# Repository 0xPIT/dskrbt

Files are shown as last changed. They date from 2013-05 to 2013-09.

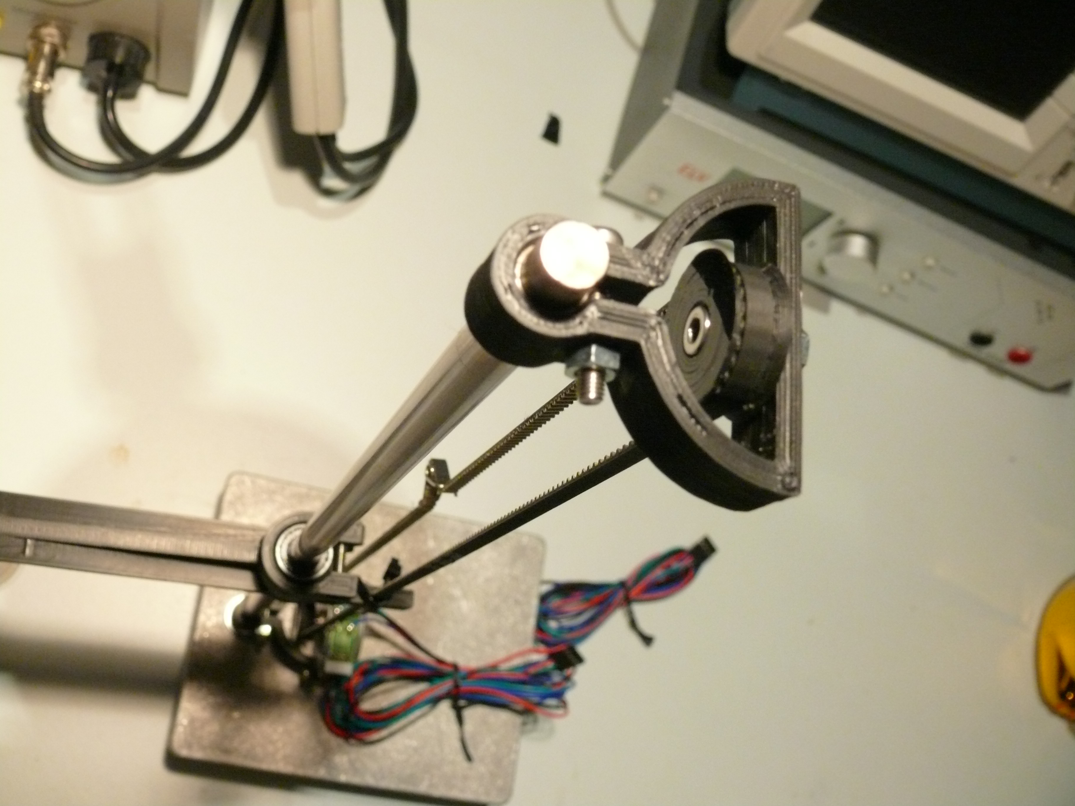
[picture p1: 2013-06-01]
photos/P1020513.JPG

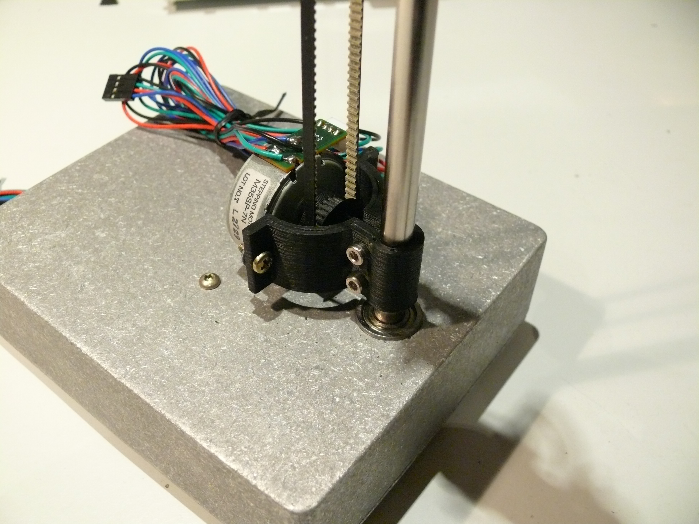
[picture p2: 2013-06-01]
photos/P1020511.JPG

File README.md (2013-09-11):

# dskrbt

As Simple as Possible CD/ DVD Disk Changer Robot

`This is a work in progress`

#### License

<br />This work is licensed under a <a rel="license" href="http://creativecommons.org/licenses/by-nc-sa/3.0/deed.en_US">Creative Commons Attribution-NonCommercial-ShareAlike 3.0 Unported License</a>.

#### Project sources

- https://github.com/0xPIT/dskrbt
- http://www.thingiverse.com/thing:97291

### What?

I intend to archive all of my several hundred audio CDs to gain shelf space. So I try to build a small robot capable of changing the disks that

- uses as few parts as possible
- can be built from cheap, standard or scrap-, plus some 3D printed parts
- is of small size so that it can be stowed away easily

Status
Status

### Design

Like most commercial units, I believe that a beam with a grabber mechanism should work best and helps to get a rather small unit. I was thinking about a suitable mechanism for grabing, that is easy to build but found no satisfactory solution. There's a project available using a carved wooden grabber with a solenoid, but thats too fragile in my opinion, also probably heavy. After finding cheap industrial vacuum cups on ebay (10€), I decided to go with that.

#### Parts used (so far)

- 8mm rod from old printer
- GT2 timing belt from old scanner for Z axis
- smaller GT2 timing belt for X (rotational) axis
- 3D-printed belt pulleys
  - find several openscad pulleys on thingiverse
- ball bearings, one flanged (F688ZZ), one normal (608)
- tiny ball bearing pressed into the idler pulley
- 3D-printed bearing holder (inside enclosure)
- cheapo aluminum enclosure
- industrial vacuum cup with spring [ebay](http://www.ebay.de/itm/160774763977) + [ebay](http://www.ebay.de/itm/160776083251)
- two stepper motors from old scanners
  - Mitsumi M35SP-7N, 4 Ohms, set to ~500mA
  - Motor pinions fit GT2 belt
- [Crumbuino](http://chip45.de/products/crumbuino-nano_arduino_compatible_atmega328_module_board_usb.php), similar to an Arduino Nano
- 2 pololu / StepStick stepper controller [ebay](http://www.ebay.de/itm/280877891763)
- [grbl](https://github.com/grbl/grbl) 0.9x to control the beast

### Issues & Todo

- Find a nice, simple way to sense that the arm has arrived at the stack of CDs while moving down the z-axis. 
  - The vacuum cup has a spring, probably add some optical or hall sensor to detect when the spirng engages? (could be too much force, though)

- Homing
  - X-Axis: Add a magnet on the motor and a Hall Sensor
  - Z-Axis: Hall or optical?

- Modify grbl and add a G-Code (M66?) so that, while picking up or dropping of a disc the arm's z-axis can move an arbitrary distance, depending on the size of stack of discs left to pick up or already dropped off.
 
- Need a method on how to detect the presence of a disk. Current draft idea is to use CNY70 refelctive optical sensor. Should simply trigger an interrrupt and send some short ascii token via the serial connection.

- The linear bearing (LM8UU) does not like the forces indiced by the changer arm and sometimes gets stuck. This is probably due to my bearing being a cheap chinese type. Use a brass or sintered bronce bearing?

- In order to save parts and a second rod, I intended the arm to be stabilized rotationally only by the belt. this is very inaccurate, the arm wiggles. could work, though.

- The vacuum cup just needs a pneumatic solenoid valve to hold a CD, i.e. no vacuum is necessary, but it wont hold for long. Therefore, I plan to use a tiny vacuum pump nevertheless.

### Status
- 2013-08-27
  - avr & pololus replaced, devised simple robot arm calibration strategy
- 2013-05-31
  - tested mechanics with grbl. works nicely. Set motors to ~500mA each.
  - messed with the cables: fried avr and pololus (got 12V on VDD)
  - Ordered replacements
- 2013-05-30
    - completed mechanical prototype

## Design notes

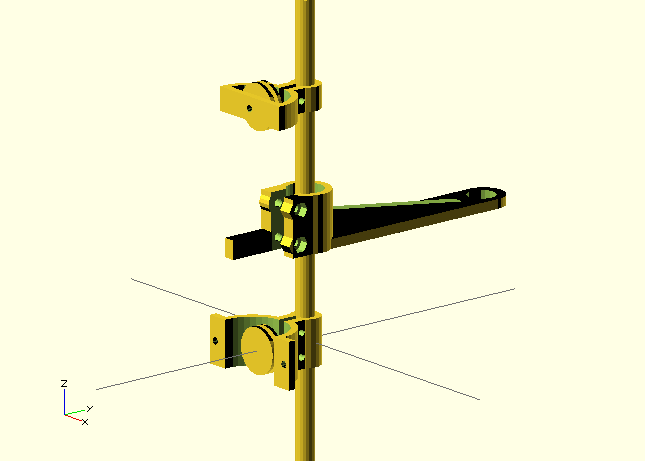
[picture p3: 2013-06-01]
mechanical/dskrbt.rendering.png

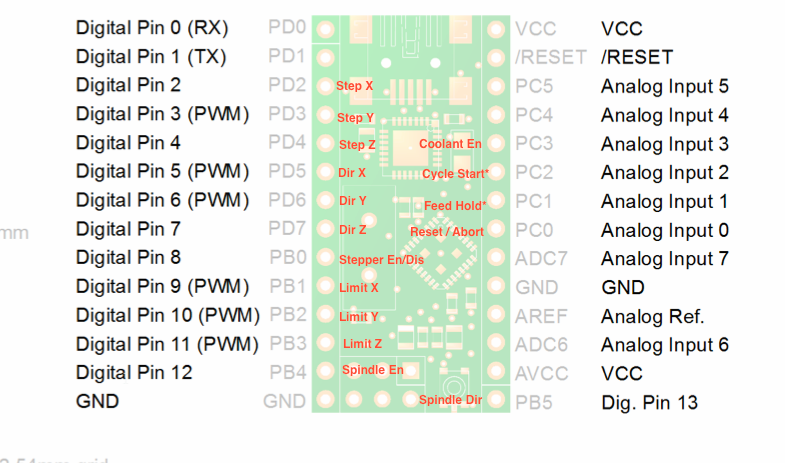
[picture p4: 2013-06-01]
misc/Crumb grmbl Pins.png

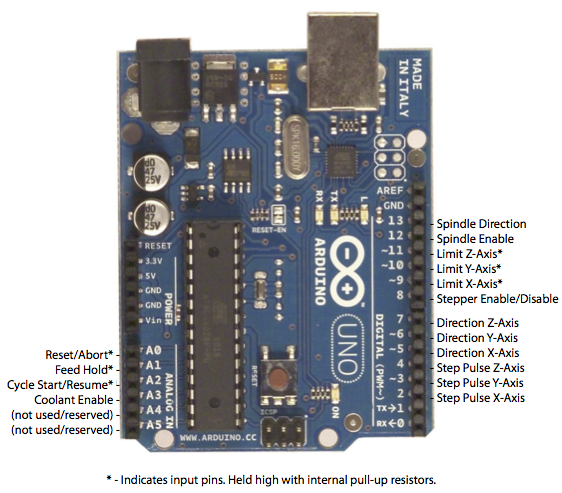
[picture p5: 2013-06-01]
misc/Grbl_Pin_Diagram.png

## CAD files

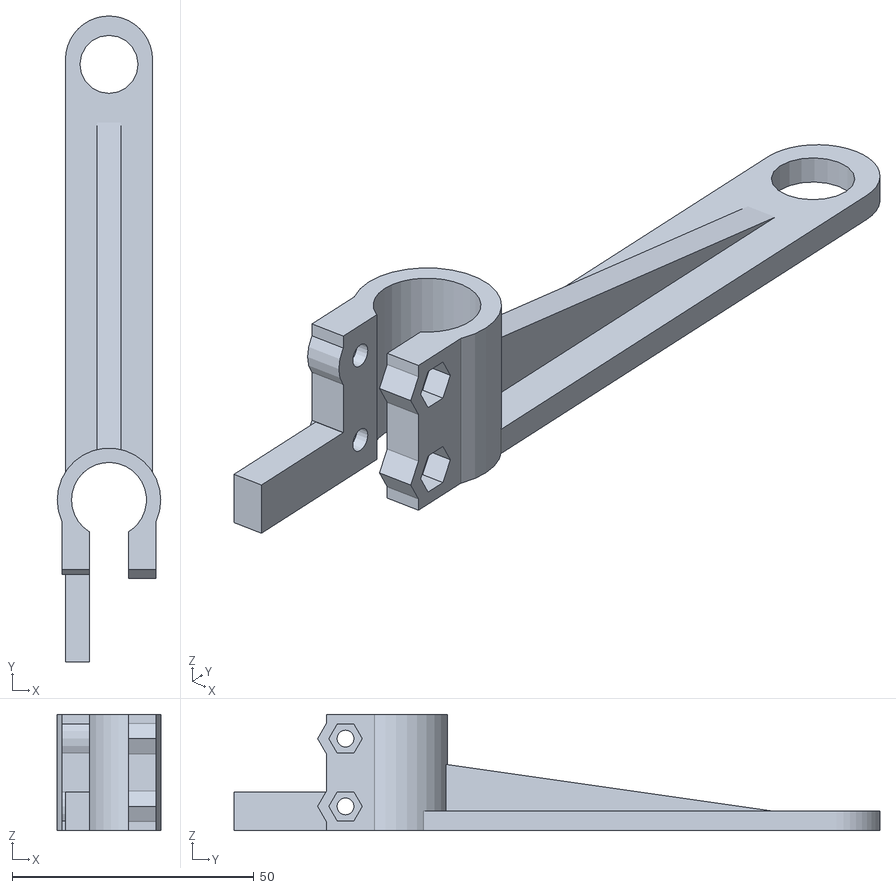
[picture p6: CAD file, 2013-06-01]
misc/carriage.stl
21.4 x 133.5 x 24.0

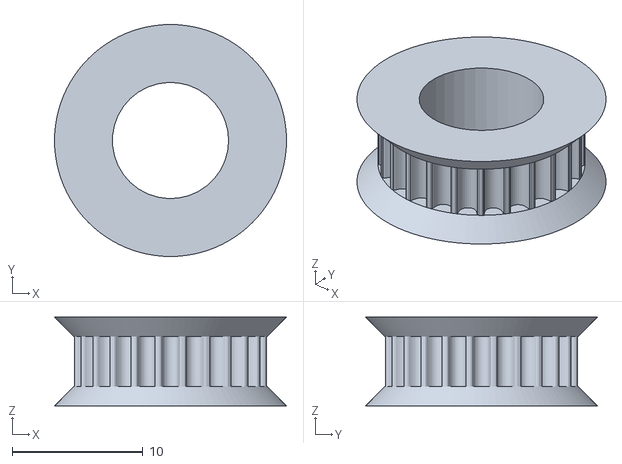
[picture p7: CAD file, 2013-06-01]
misc/PulleyMotor.stl
17.8 x 17.8 x 6.80

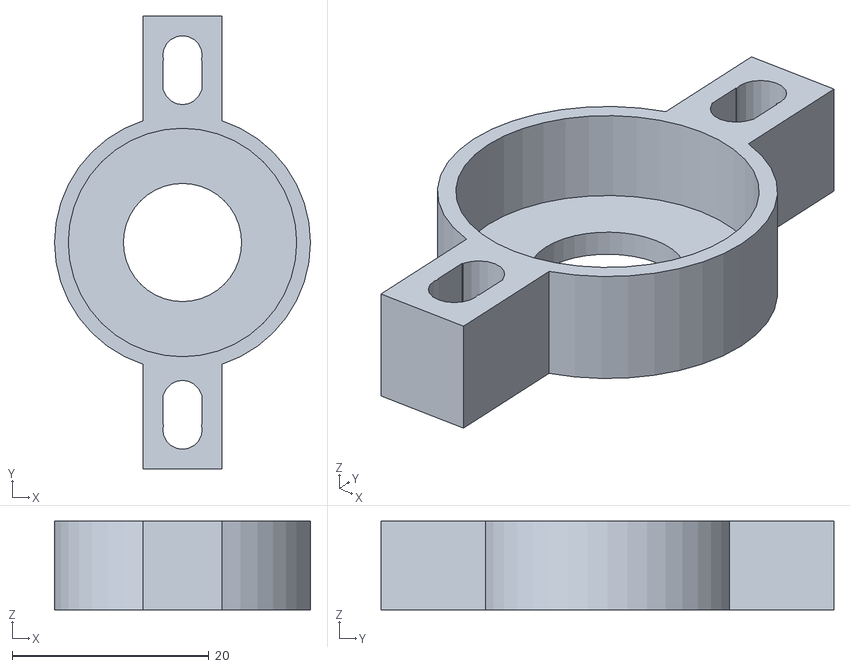
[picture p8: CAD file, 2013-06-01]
misc/608mount.stl
26.0 x 46.0 x 9.00

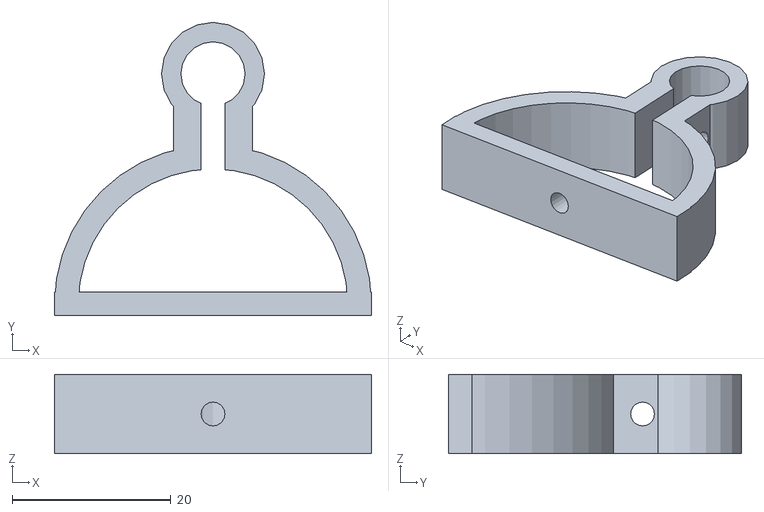
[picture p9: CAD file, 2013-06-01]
misc/mount_top.stl
40.0 x 37.0 x 10.0

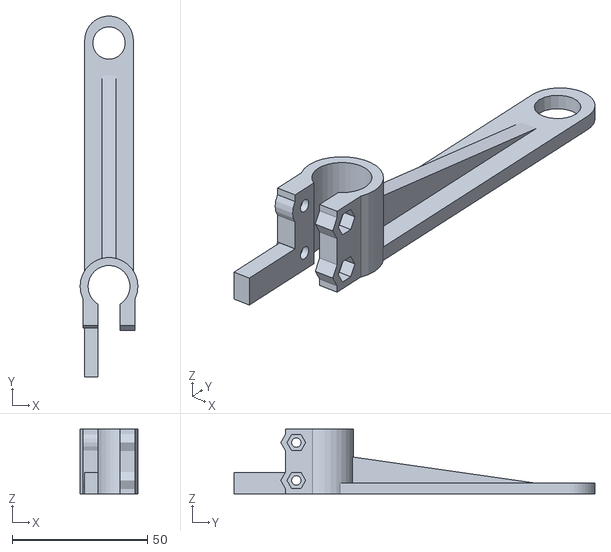
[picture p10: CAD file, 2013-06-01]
misc/carriage_fixed.stl
21.4 x 133.5 x 24.0

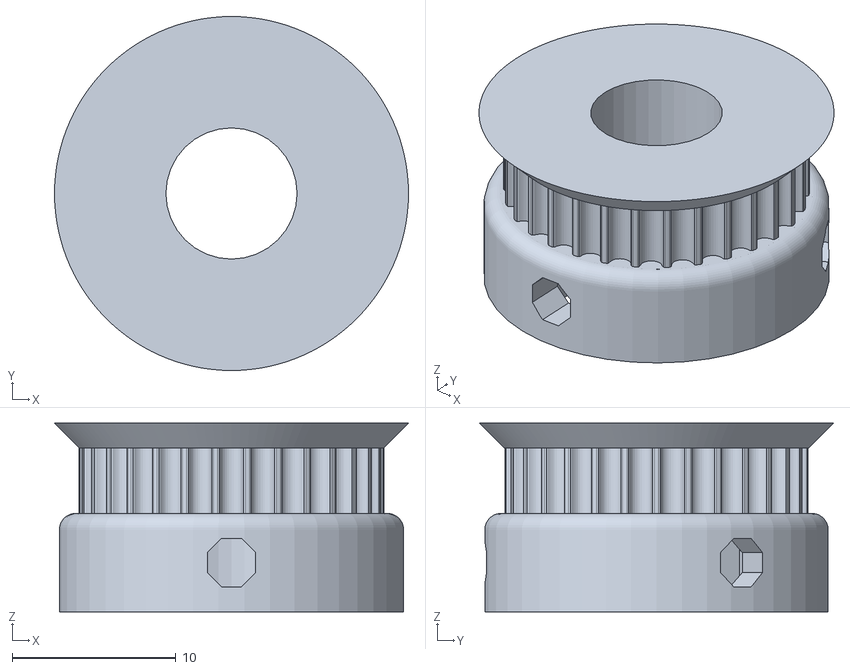
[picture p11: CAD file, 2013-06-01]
misc/Pulley_GT2_30T_8mm.stl
21.6 x 21.6 x 11.5

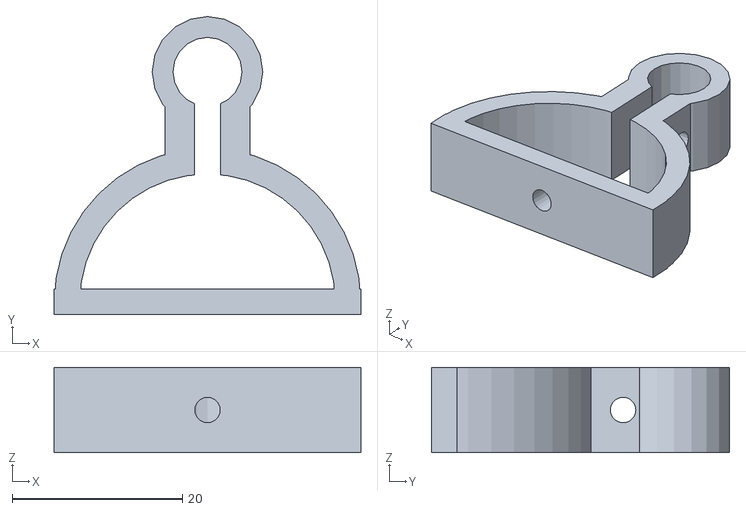
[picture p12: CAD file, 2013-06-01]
misc/mountIdler.stl
36.0 x 35.0 x 10.0

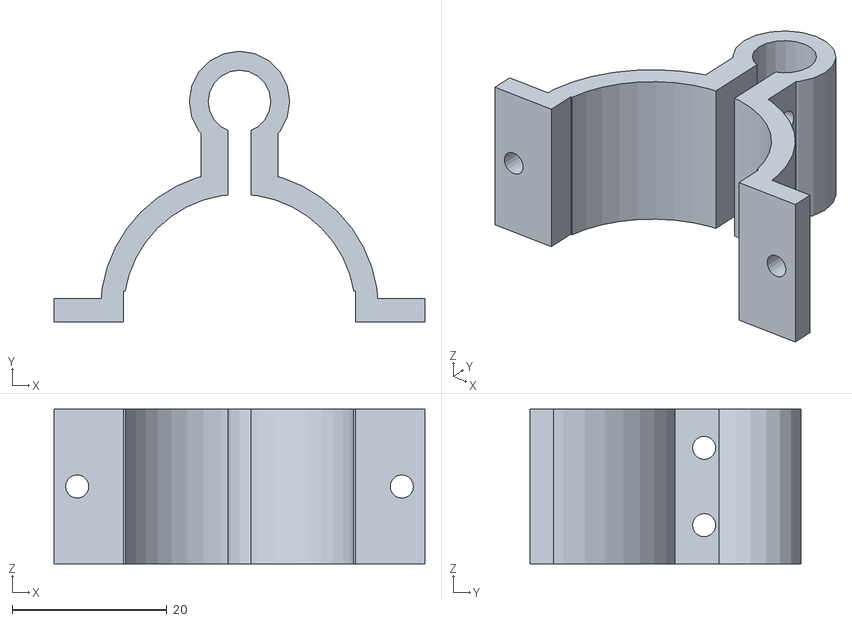
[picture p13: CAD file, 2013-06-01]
misc/mountMotor.stl
48.0 x 35.0 x 20.0

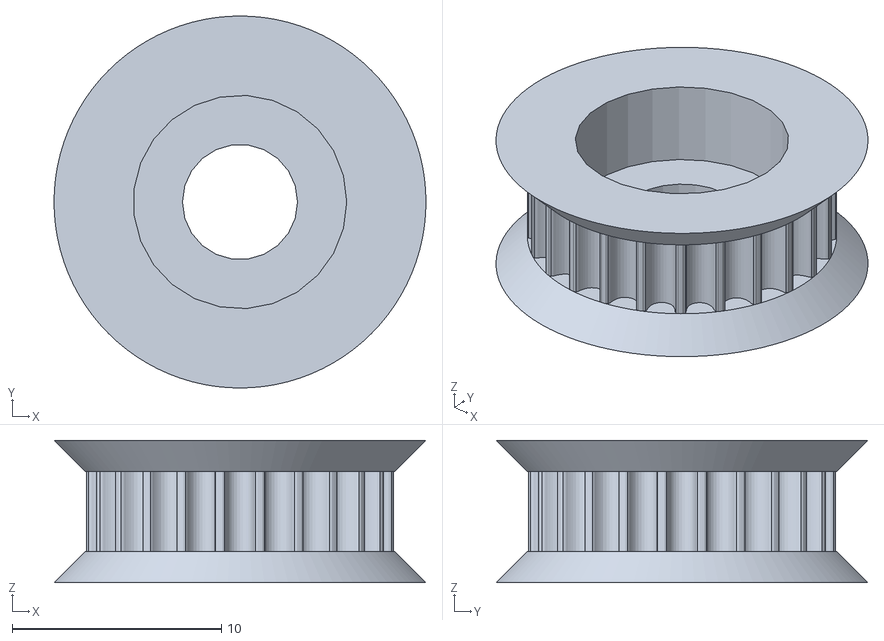
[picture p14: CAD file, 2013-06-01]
misc/PulleyIdler.stl
17.8 x 17.8 x 6.80

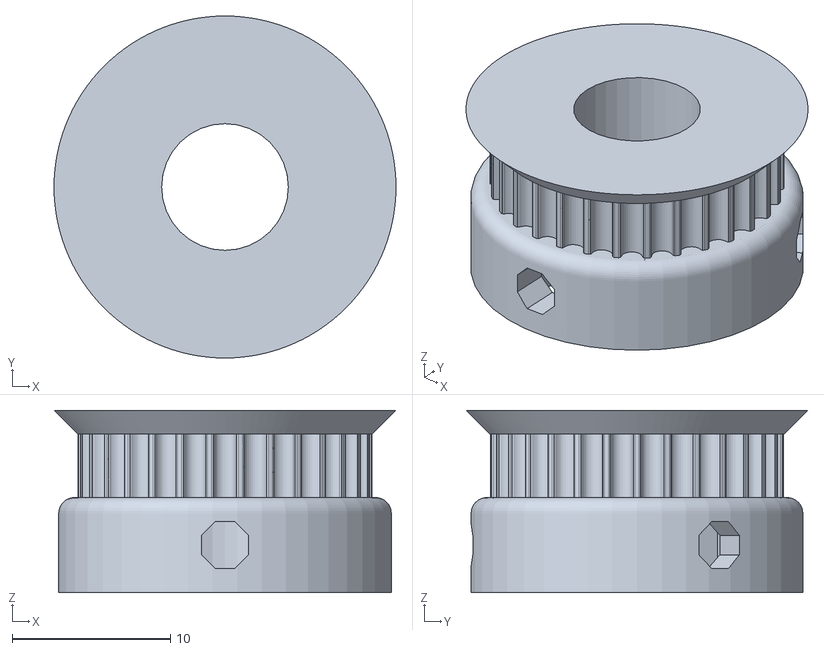
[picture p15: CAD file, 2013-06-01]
misc/PulleyGT230T8mm_fixed.stl
21.6 x 21.6 x 11.5

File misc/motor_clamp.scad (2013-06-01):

$fa = 12;
$fs = 0.5;

w = 60; // Smooth rod distance (center to center)

module screws() {
  for (x = [-w/2, w/2]) {
    translate([x, 0, 0]) {
      // Push-through M3 screw hole.
      translate([0, -6, 0]) rotate([0, 90, 0])
	cylinder(r=1.65, h=20, center=true);
      // M3 nut holder.
      translate([-x/5, -6, 0])
	rotate([30, 0, 0]) rotate([0, 90, 0])
	cylinder(r=3.3, h=2.3, center=true, $fn=6);
    }
  }
}

module bracket(h) {
  difference() {

    union() {
      translate([0, -1, 0]) cube([w+12, 22, h], center=true);
      // Sandwich mount.
      translate([-w/2, 10, 0]) cylinder(r=6, h=h, center=true);
      translate([w/2, 10, 0]) cylinder(r=6, h=h, center=true);
    }

    // Sandwich mount.
    translate([-w/2, 12, 0]) cylinder(r=1.9, h=h+1, center=true);
    translate([w/2, 12, 0]) cylinder(r=1.9, h=h+1, center=true);

    // Smooth rod mounting slots.
    for (x = [-w/2, w/2]) {
      translate([x, 0, 0]) {
      	cylinder(r=3.1, h=h+1, center=true);
	    translate([0, -10, 0]) cube([2, 20, h+1], center=true);
      }
    }

    // Belt path.
    translate([0, -5, 0]) cube([w-20, 20, h+1], center=true);
    translate([0, -9, 0]) cube([w-12, 20, h+1], center=true);
    translate([-w/2+10, 1, 0]) cylinder(r=4, h=h+1, center=true);
    translate([w/2-10, 1, 0]) cylinder(r=4, h=h+1, center=true);
  }
}

translate([0, 0, 10]) 
difference() {
bracket(20);
screws();
}

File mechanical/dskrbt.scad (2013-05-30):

// ----------------------------------------------------------------------
// Disk Changer Robot
// github.com/0xPIT/dskrbt
// (c) 2013 karl@pitrich.com
// Insert Creative Commons License Terms Here
// 
// Credits:
//   * modified LM8UU holder by Jonas Kühling
// ----------------------------------------------------------------------

include <./MCAD/shapes.scad>
include <./MCAD/regular_shapes.scad>
include <./MCAD/boxes.scad>

aluminum = [0.9, 0.9, 0.9];
steel = [0.8, 0.8, 0.9];


LM8UU_dia = 15.4; // must be wider than bearing and adjust for printer
LM8UU_length = 24;
rod_dia = 6;

//screw/nut dimensions (M3) - hexagon socket head cap screw ISO 4762, hexagon nut ISO 4032
screw_thread_dia_iso = 3;
screw_head_dia_iso = 5.5;
nut_wrench_size_iso = 5.5;

// screw/nut dimensions for use (plus clearance for fitting purpose)
clearance_dia = 0.5;
screw_thread_dia = screw_thread_dia_iso + clearance_dia;
screw_head_dia = screw_head_dia_iso + clearance_dia;
nut_wrench_size = nut_wrench_size_iso + clearance_dia;
nut_dia_perimeter = (nut_wrench_size/cos(30));
nut_dia = nut_dia_perimeter;
nut_surround_thickness = 2;

// main body dimensions
body_wall_thickness = 2;
body_width = LM8UU_dia + (2*body_wall_thickness);
body_height = body_width;
body_length = LM8UU_length;
gap_width = rod_dia + 2;
screw_bushing_space = 1;

screw_elevation = LM8UU_dia + body_wall_thickness + screw_thread_dia / 2 + screw_bushing_space;

motor_holes    =  42;
arm_length     =  100;
stabilizer_pos = -60;
mount_length   =  60;

module carriage() {
  union() 
  {
    translate([0, LM8UU_dia/2 + body_wall_thickness, 0])
      rotate([90, 0, 0]) 
        lm8uu_holder();

    difference() {
      union() {
        translate([0, (arm_length / 2) - 4.5, -LM8UU_length/2 + 2])
          cube([18, arm_length - 9, 4], center=true);
        
        translate([0, arm_length - 9, -LM8UU_length/2 + 2]) 
          cylinder(r=9, h=4, center=true, $fn=40);
        
        // arm stabilizer
        translate([0, 8, -8])
          rotate([90, 0, -90])
            rightTriangle(arm_length/100*70, 10, 5);
      }

      // cut out inner cylinder
	  translate([0, 0, -(LM8UU_length + 1) / 2]) 
        polyhole(LM8UU_dia, LM8UU_length + 1);

      // payload bore
      translate([0, arm_length - 10, -10])
        cylinder(r=6, h=10, center=true, $fn=20);
    }

    difference() {
      union() {
        translate([-6.5, -23.5, -LM8UU_length/2 + 4])
          cube([5, 20, 8], center=true);
        //translate([-4, stabilizer_pos, -LM8UU_length/2 + 4])
        //  cube([8, 8, 8], center=true);
      }
      //translate([-4, stabilizer_pos, -8])
      //  cylinder(r=1.5, h=10, center=true, $fn=20);
    }
  }
}


module edgeMount(height, upper=false) 
{
  difference() {
    union() {
      cylinder(r=6.5, h=height, center=true, $fn=20);

      for(i = [3, -3])
        translate([i, -5, 0])
          cube([4, 10, height], center=true);

      translate([0, -27, 0]) 
        union() {
          intersection() {
            cylinder_tube(20, 18, 3, center=true, $fn=40);
            translate([0, 10, 0])
              cube([50, 20, height], center=true);
          }

		  if (upper)
            cube([18 * 2, 3, height], center=true);
          if (!upper)
            cube([motor_holes+6, 3, height], center=true);          
        }
    }

    // clamp screw mount holes
    for(i=[height / 2 - 5, -height / 2 + 5])
      translate([0, -6, i])
        rotate([0, 90, 0])
          cylinder(r=1.5, h=15, center=true, $fn=20);

    // rod bore
    cylinder(r=4.05, h=height, center=true, $fn=20);

    // split
    translate([0, -10, 0]) cube([3, 20, height], center=true); 
    if (!upper) {
      translate([0, -27, 0]) cube([18 * 2 - 6, 5, height], center=true);
      translate([0, -40, 0]) rotate([90, 90, 180]) motor42(false);
    }
    else { // upper: bore for pulley
      translate([0, -30, 0]) rotate([90, 0, 0]) cylinder(r=1.5, h=10, center=true, $fn=20);
    }
  }  
}


module motor42(with_body = true) {
    if (with_body)
      cylinder(r=21, h=16, center=true, $fn=20);

    // motor mount holes
    for(i=[motor_holes/2, -motor_holes/2])
      translate([0, i, 10])
          cylinder(r=1.5, h=10+2, center=true, $fn=20);

    // motor shaft hole
    translate([0, 0, 10])
        cylinder(r=5, h=10+2, center=true, $fn=20);
}


module motorCutOut() {  
  difference() {
    cylinder(r=17, h=6, center=true, $fn=20);
    cylinder(r=10, h=6, center=true, $fn=20);
    cube([40, 6, 4] ,center=true);
    cube([6, 40, 4] ,center=true);
  }
}


module rods() {
  // main rod
  translate([0, 0, -60])  color(steel) cylinder(r=4, h=200, center=false, $fn=20);

  // stabilizer rod
  //translate([-4, stabilizer_pos, -60])  color(steel) cylinder(r=1.5, h=400, center=false, $fn=20);
}


module compactDisc() {
  color([0, 1.0, 0]) 
    difference() {
      cylinder(r=60,  h=1, center=true, $fn=20);
      cylinder(r=7.5, h=1, center=true, $fn=20);  
    }
}


// nophead's polyhole module for better lm8uu-fit
module polyhole(d,h) {
    n = max(round(2 * d),3);
    rotate([0,0,180])
        cylinder(h = h, r = (d / 2) / cos (180 / n), $fn = n);
}


module mount_plate() {
  difference() {
    translate([0,0,1.5])
	  cube([body_width + 2 * screw_head_dia + 4 * nut_surround_thickness, screw_head_dia + 2 * nut_surround_thickness, 3], center=true);
		for(i = [-1, 1])
			translate([i * (body_width / 2 + nut_surround_thickness + screw_head_dia / 2), 0, -0.5])
              cylinder(r=screw_thread_dia / 2, h=4, $fn=20);
	}
}

// main body
module lm8uu_holder(with_mountplate=false, dia=LM8UU_dia)
{
	difference() {
		union() {
			if (with_mountplate) 
				mount_plate();
	
			// body
			//translate([0,0,body_height/4])
			//	cube([body_width,body_length,body_height/2], center=true);
			translate([0,0,(dia/2)+body_wall_thickness])		
				rotate([90,0,0])
					cylinder(r=(dia/2) + body_wall_thickness+1, h=LM8UU_length, center=true);
	
			// gap support
			translate([-(gap_width/2)-body_wall_thickness,-(body_length/2),body_height/2])
				cube([body_wall_thickness,LM8UU_length,(dia/2)+screw_bushing_space+(screw_thread_dia/2)]);
			translate([gap_width/2,-(body_length/2),body_height/2])
				cube([body_wall_thickness,LM8UU_length,(dia/2)+screw_bushing_space+(screw_thread_dia/2)]);
	
	
			// nut trap surround

			translate([gap_width/2, -7, screw_elevation])
				rotate([0,90,0])
					cylinder(r=(((nut_wrench_size+nut_surround_thickness*2)/cos(30))/2), h=(body_width-gap_width)/2, $fn=6);


			translate([gap_width/2, 7, screw_elevation])
				rotate([0,90,0])
					cylinder(r=(((nut_wrench_size+nut_surround_thickness*2)/cos(30))/2), h=(body_width-gap_width)/2, $fn=6);


			translate([gap_width/2 + (body_width-gap_width)/4, 
						0, 
						screw_elevation - 2])
				cube([ (body_width - gap_width)/2,
						LM8UU_length,
						nut_dia_perimeter + 5  ],
						center=true);


			// Screw hole surround

			translate([-gap_width/2, -7, screw_elevation])
				rotate([0,-90,0])
					cylinder(r=(screw_head_dia/2)+nut_surround_thickness, h=(body_width-gap_width)/2, $fn=20);

	translate([-gap_width/2, 7, screw_elevation])
				rotate([0,-90,0])
					cylinder(r=(screw_head_dia/2)+nut_surround_thickness, h=(body_width-gap_width)/2, $fn=20);

	translate([-(gap_width / 2 + (body_width - gap_width) / 4), 
				0,
				screw_elevation -2 ])
		cube([(body_width - gap_width) / 2,
			LM8UU_length,
			nut_dia_perimeter + 5],
			center=true);

		}
	
		// bushing hole
		translate([0, 0, dia / 2 + 2])
			rotate([90, 0, 0])
				translate([0, 0, -(LM8UU_length + 1) / 2]) polyhole(dia, LM8UU_length + 1);
	
		// top gap
		translate([
			-(gap_width / 2),
			-(body_length / 2) - 1,
			body_height / 2]
		)
			cube([gap_width,
				  LM8UU_length + 2,
				  (dia / 2) + screw_bushing_space + (screw_thread_dia / 2) + (nut_dia / 2) + nut_surround_thickness + 1]);


		// screw holes (one all the way through)
		translate([0, -7, screw_elevation])
			rotate([0, 90, 0])
				cylinder(r=screw_thread_dia/2, h=body_width+3, center=true, $fn=20);

		// screw hole (one all the way through)
		translate([0, 7, screw_elevation])
			rotate([0,90,0])
				cylinder(r=screw_thread_dia/2, h=body_width+3, center=true, $fn=20);
	
		// nut trap
		translate([gap_width/2+body_wall_thickness,-7,screw_elevation])
			rotate([0,90,0])
				cylinder(r=nut_dia/2, h=body_width/2-gap_width/2-body_wall_thickness+1,$fn=6);

		translate([gap_width/2+body_wall_thickness,7,screw_elevation])
			rotate([0,90,0])
				cylinder(r=nut_dia/2, h=body_width/2-gap_width/2-body_wall_thickness+1,$fn=6);

	
		// screw head hole
		translate([-(gap_width)/2-body_wall_thickness,-7,screw_elevation])
			rotate([0,-90,0])
				cylinder(r=screw_head_dia/2, h=body_width/2-gap_width/2-body_wall_thickness+1,$fn=20);
		translate([-(gap_width)/2-body_wall_thickness,7,screw_elevation])
			rotate([0,-90,0])
				cylinder(r=screw_head_dia/2, h=body_width/2-gap_width/2-body_wall_thickness+1,$fn=20);
	
	}
}
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

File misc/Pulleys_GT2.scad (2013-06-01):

// Parametric Pulley with multiple belt profiles
// by droftarts January 2012

// Based on pulleys by:
// http://www.thingiverse.com/thing:11256 by me!
// https://github.com/prusajr/PrusaMendel by Josef Prusa
// http://www.thingiverse.com/thing:3104 by GilesBathgate
// http://www.thingiverse.com/thing:2079 by nophead

// dxf tooth data from http://oem.cadregister.com/asp/PPOW_Entry.asp?company=915217&elementID=07807803/METRIC/URETH/WV0025/F
// pulley diameter checked and modelled from data at http://www.sdp-si.com/D265/HTML/D265T016.html

/**
 * @name Pulley
 * @category Printed
 * @using 1 x m3 nut, normal or nyloc
 * @using 1 x m3x10 set screw or 1 x m3x8 grub screw
 */


// tuneable constants

teeth = 24;			// Number of teeth, standard Mendel T5 belt = 8, gives Outside Diameter of 11.88mm
profile = 12;		// 1=MXL 2=40DP 3=XL 4=H 5=T2.5 6=T5 7=T10 8=AT5 9=HTD_3mm 10=HTD_5mm 11=HTD_8mm 12=GT2_2mm 13=GT2_3mm 14=GT2_5mm

motor_shaft =8.9;	    // NEMA17 motor shaft exact diameter = 5
m3_dia = 3.2;		// 3mm hole diameter
m3_nut_hex = 1;		// 1 for hex, 0 for square nut
m3_nut_flats = 5.7;	// normal M3 hex nut exact width = 5.5
m3_nut_depth = 2.7;	// normal M3 hex nut exact depth = 2.4, nyloc = 4

retainer = 1;		// Belt retainer above teeth, 0 = No, 1 = Yes
retainer_ht = 1.5;	// height of retainer flange over pulley, standard = 1.5
idler = 1;			// Belt retainer below teeth, 0 = No, 1 = Yes
idler_ht = 1.5;		// height of idler flange over pulley, standard = 1.5

pulley_t_ht = 3.8;	// length of toothed part of pulley, standard = 12
pulley_b_ht = 1.5;		// pulley base height, standard = 8. Set to same as idler_ht if you want an idler but no pulley.
pulley_b_dia = 20;	// pulley base diameter, standard = 20
no_of_nuts = 1;		// number of captive nuts required, standard = 1
nut_angle = 90;		// angle between nuts, standard = 90
nut_shaft_distance = 1.2;	// distance between inner face of nut and shaft, can be negative.


//	********************************
//	** Scaling tooth for good fit **
//	********************************
/*	To improve fit of belt to pulley, set the following constant. Decrease or increase by 0.1mm at a time. We are modelling the *BELT* tooth here, not the tooth on the pulley. Increasing the number will *decrease* the pulley tooth size. Increasing the tooth width will also scale proportionately the tooth depth, to maintain the shape of the tooth, and increase how far into the pulley the tooth is indented. Can be negative */

additional_tooth_width = 0.2; //mm

//	If you need more tooth depth than this provides, adjust the following constant. However, this will cause the shape of the tooth to change.

additional_tooth_depth = 0.2; //mm

// calculated constants

nut_elevation = pulley_b_ht/2;
m3_nut_points = 2*((m3_nut_flats/2)/cos(30)); // This is needed for the nut trap

// The following set the pulley diameter for a given number of teeth

MXL_pulley_dia = tooth_spacing (2.032,0.254);
40DP_pulley_dia = tooth_spacing (2.07264,0.1778);
XL_pulley_dia = tooth_spacing (5.08,0.254);
H_pulley_dia = tooth_spacing (9.525,0.381);
T2_5_pulley_dia = tooth_spaceing_curvefit (0.7467,0.796,1.026);
T5_pulley_dia = tooth_spaceing_curvefit (0.6523,1.591,1.064);
T10_pulley_dia = tooth_spacing (10,0.93);
AT5_pulley_dia = tooth_spaceing_curvefit (0.6523,1.591,1.064);
HTD_3mm_pulley_dia = tooth_spacing (3,0.381);
HTD_5mm_pulley_dia = tooth_spacing (5,0.5715);
HTD_8mm_pulley_dia = tooth_spacing (8,0.6858);
GT2_2mm_pulley_dia = tooth_spacing (2,0.254);
GT2_3mm_pulley_dia = tooth_spacing (3,0.381);
GT2_5mm_pulley_dia = tooth_spacing (5,0.5715);

// The following calls the pulley creation part, and passes the pulley diameter and tooth width to that module

if ( profile == 1 ) { pulley ( "MXL" , MXL_pulley_dia , 0.508 , 1.321 ); }
if ( profile == 2 ) { pulley ( "40 D.P." , 40DP_pulley_dia , 0.457 , 1.226 ); }
if ( profile == 3 ) { pulley ( "XL" , XL_pulley_dia , 1.27, 3.051 ); }
if ( profile == 4 ) { pulley ( "H" , H_pulley_dia ,1.905 , 5.359 ); }
if ( profile == 5 ) { pulley ( "T2.5" , T2_5_pulley_dia , 0.7 , 1.678 ); }
if ( profile == 6 ) { pulley ( "T5" , T5_pulley_dia , 1.19 , 3.264 ); }
if ( profile == 7 ) { pulley ( "T10" , T10_pulley_dia , 2.5 , 6.13 ); }
if ( profile == 8 ) { pulley ( "AT5" , AT5_pulley_dia , 1.19 , 4.268 ); }
if ( profile == 9 ) { pulley ( "HTD 3mm" , HTD_3mm_pulley_dia , 1.289 , 2.27 ); }
if ( profile == 10 ) { pulley ( "HTD 5mm" , HTD_5mm_pulley_dia , 2.199 , 3.781 ); }
if ( profile == 11 ) { pulley ( "HTD 8mm" , HTD_8mm_pulley_dia , 3.607 , 6.603 ); }

if ( profile == 12 ) 
{ 
  difference() {
    pulley ( "GT2 2mm" , GT2_2mm_pulley_dia , 0.764 , 1.494 ); 
    //translate([0, 0, 4.8]) cylinder(r=5.1, h=4, $fn=25, center=true);
  }
}

if ( profile == 13 ) { pulley ( "GT2 3mm" , GT2_3mm_pulley_dia , 1.169 , 2.31 ); }
if ( profile == 14 ) { pulley ( "GT2 5mm" , GT2_5mm_pulley_dia , 1.969 , 3.952 ); }

// Functions

function tooth_spaceing_curvefit (b,c,d)
	= ((c * pow(teeth,d)) / (b + pow(teeth,d))) * teeth ;

function tooth_spacing(tooth_pitch,pitch_line_offset)
	= (2*((teeth*tooth_pitch)/(3.14159265*2)-pitch_line_offset)) ;

// Main Module

module pulley( belt_type , pulley_OD , tooth_depth , tooth_width )
	{
	echo (str("Belt type = ",belt_type,"; Number of teeth = ",teeth,"; Pulley Outside Diameter = ",pulley_OD,"mm "));
	tooth_distance_from_centre = sqrt( pow(pulley_OD/2,2) - pow((tooth_width+additional_tooth_width)/2,2));
	tooth_width_scale = (tooth_width + additional_tooth_width ) / tooth_width;
	tooth_depth_scale = ((tooth_depth + additional_tooth_depth ) / tooth_depth) ;


//	************************************************************************
//	*** uncomment the following line if pulley is wider than puller base ***
//	************************************************************************

//	translate ([0,0, pulley_b_ht + pulley_t_ht + retainer_ht ]) rotate ([0,180,0])

	difference()
	 {	 
		union()
		{
			//base
	
			if ( pulley_b_ht < 2 ) { echo ("CAN'T DRAW PULLEY BASE, HEIGHT LESS THAN 2!!!"); } else {
				rotate_extrude($fn=pulley_b_dia*2)
				{
						square([pulley_b_dia/2-1,pulley_b_ht]);
						square([pulley_b_dia/2,pulley_b_ht-1]);
						translate([pulley_b_dia/2-1,pulley_b_ht-1]) circle(1);
				}
			}
	
		difference()
			{
			//shaft - diameter is outside diameter of pulley
			
			translate([0,0,pulley_b_ht]) 
			rotate ([0,0,360/(teeth*4)]) 
			cylinder(r=pulley_OD/2,h=pulley_t_ht, $fn=teeth*4);
	
			//teeth - cut out of shaft
		
			for(i=[1:teeth]) 
			rotate([0,0,i*(360/teeth)])
			translate([0,-tooth_distance_from_centre,pulley_b_ht -1]) 
			scale ([ tooth_width_scale , tooth_depth_scale , 1 ]) 
			{
			if ( profile == 1 ) { MXL();}
			if ( profile == 2 ) { 40DP();}
			if ( profile == 3 ) { XL();}
			if ( profile == 4 ) { H();}
			if ( profile == 5 ) { T2_5();}
			if ( profile == 6 ) { T5();}
			if ( profile == 7 ) { T10();}
			if ( profile == 8 ) { AT5();}
			if ( profile == 9 ) { HTD_3mm();}
			if ( profile == 10 ) { HTD_5mm();}
			if ( profile == 11 ) { HTD_8mm();}
			if ( profile == 12 ) { GT2_2mm();}
			if ( profile == 13 ) { GT2_3mm();}
			if ( profile == 14 ) { GT2_5mm();}
			}

			}
			
		//belt retainer / idler
		if ( retainer > 0 ) {translate ([0,0, pulley_b_ht + pulley_t_ht ]) 
		rotate_extrude($fn=teeth*4)  
		polygon([[0,0],[pulley_OD/2,0],[pulley_OD/2 + retainer_ht , retainer_ht],[0 , retainer_ht],[0,0]]);}
		
		if ( idler > 0 ) {translate ([0,0, pulley_b_ht - idler_ht ]) 
		rotate_extrude($fn=teeth*4)  
		polygon([[0,0],[pulley_OD/2 + idler_ht,0],[pulley_OD/2 , idler_ht],[0 , idler_ht],[0,0]]);}
	
		}
	   
		//hole for motor shaft
		translate([0,0,-1])cylinder(r=motor_shaft/2,h=pulley_b_ht + pulley_t_ht + retainer_ht + 2,$fn=motor_shaft*4);
				
		//captive nut and grub screw holes
	
		if ( pulley_b_ht < m3_nut_flats ) { echo ("CAN'T DRAW CAPTIVE NUTS, HEIGHT LESS THAN NUT DIAMETER!!!"); } else {
		if ( (pulley_b_dia - motor_shaft)/2 < m3_nut_depth + 3 ) { echo ("CAN'T DRAW CAPTIVE NUTS, DIAMETER TOO SMALL FOR NUT DEPTH!!!"); } else {
	
			for(j=[1:no_of_nuts]) rotate([0,0,j*nut_angle])
			translate([0,0,nut_elevation])rotate([90,0,0])
	
			union()
			{
				//entrance
				translate([0,-pulley_b_ht/4-0.5,motor_shaft/2+m3_nut_depth/2+nut_shaft_distance]) cube([m3_nut_flats,pulley_b_ht/2+1,m3_nut_depth],center=true);
	
				//nut
				if ( m3_nut_hex > 0 )
					{
						// hex nut
						translate([0,0.25,motor_shaft/2+m3_nut_depth/2+nut_shaft_distance]) rotate([0,0,30]) cylinder(r=m3_nut_points/2,h=m3_nut_depth,center=true,$fn=6);
					} else {
						// square nut
						translate([0,0.25,motor_shaft/2+m3_nut_depth/2+nut_shaft_distance]) cube([m3_nut_flats,m3_nut_flats,m3_nut_depth],center=true);
					}
	
				//grub screw hole
				rotate([0,0,22.5])cylinder(r=m3_dia/2,h=pulley_b_dia/2+1,$fn=8);
			}
		}}
	 }
	   
	}


// Tooth profile modules
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

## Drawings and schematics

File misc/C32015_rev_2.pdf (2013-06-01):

## Microstep Selection (1= Jumper On)

## Full Step No Jumpers

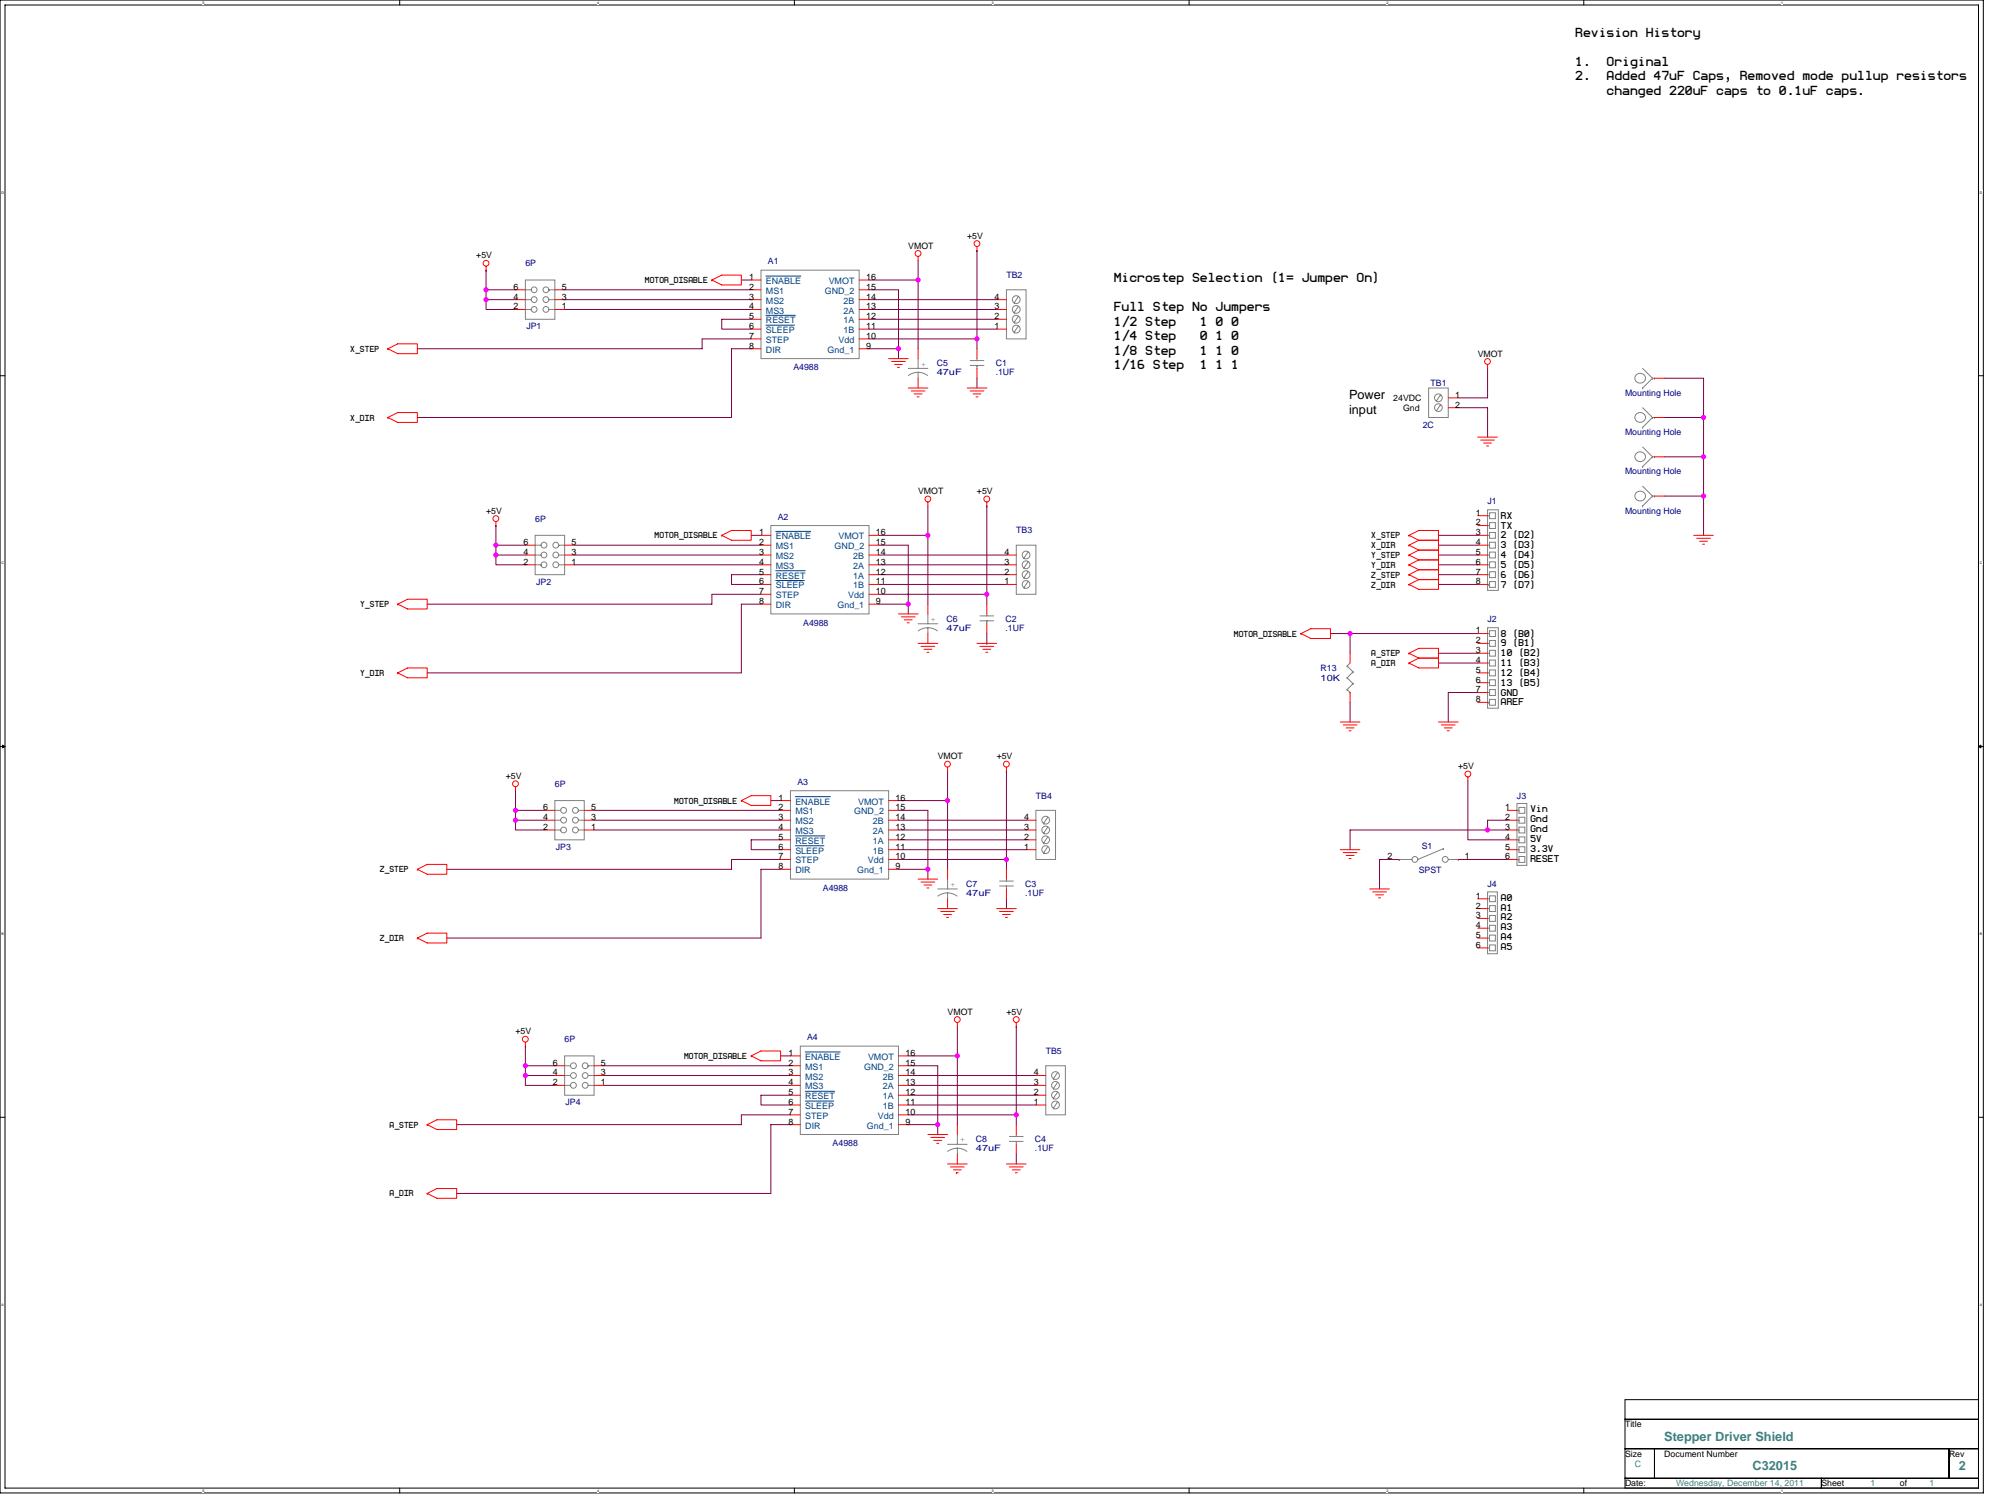
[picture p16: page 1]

1. Original
2. Added 47uF Caps, Removed mode pullup resistors
changed 220uF caps to 0.1uF caps.

RESET 5 | 2
SLEEP 6 | 1

RESET 5 | | 2
SLEEP 6 | | | 1

Size C | Document Number C32015 | Rev 2

Date: Wednesday, December 14, 2011 | Sheet 1 of 1

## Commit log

2013-05-30 add scad file
    [cdrbt.scad]
2013-06-01 add current status
    [608mount.stl, PulleyGT230T8mm_fixed.stl, PulleyIdler.stl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]
